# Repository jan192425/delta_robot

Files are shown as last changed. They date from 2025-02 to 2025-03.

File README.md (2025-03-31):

# Aufbau einer Compliant-Delta-Kinematik für die intuitive Interaktion mit einem Mobilen Roboter

Nachfolgend ist die Projektarbeit von Jan Sopejstal, Thomas Tasler und Nick Müller beschrieben. Die Arbeit wurde im Wintersemester 24/25 an der Technischen Hochschule Nürnberg Georg Simon Ohm durchgeführt und von Herrn Prof. Dr. rer. nat. Christian Pfitzner betreut.

## Inhaltsverzeichnis

- [1. Projektbeschreibung / Ziel des Projektes](#1-projektbeschreibung--ziel-des-projektes)
- [2. Komponenten des Delta-Pickers](#2-komponenten-des-delta-pickers)
- [3. Auslegung der Motoren](#3-auslegung-der-motoren)
- [4. Umsetzung der zwei Modis](#4-umsetzung-der-zwei-modis)
    - [4.1 Setup](#41-setup)
    - [4.2 Auswählbare Modi](#42-auswählbare-modi)
        - [4.2.1 Punktnavigation (mode: 0)](#421-punktnavigation-mode-0)
        - [4.2.2 Compliant-Modus (mode: 1)](#422-compliant-modus-mode-1)
- [5. Simulator für Delta-Roboter](#5-simulator-für-delta-roboter)
---

## 1. Projektbeschreibung / Ziel des Projektes
Für die Steuerung eines mobilen Robotes soll eine Delta-Kinematik aufgebaut werden. Durch eine geeignete Auswahl an Motoren und Ansteuerung soll die Kinematik einen vorgegebenen Zielpunkt anfahren können. Darüber hinaus, soll die Kinematik auch durch Interaktion in eine Richtung von Hand bewegt werden und bei eine einem Loslassen zurück in die Ursprungsposition fahren. Notwendig ist hierfür eine dynamische Regelung.<br>
Eine Video, das den gesamten Projektverlauf dokumentiert, ist unter folgendem Link zu finden: https://www.youtube.com/watch?v=dIm20Sjufmg&ab_channel=ThomasT .

## 2. Komponenten des Delta-Pickers
Der Delta-Roboter besteht grundlegend aus einer [Grundplatte](/images/base.png), [drei Baugleichen Armen](/images/arm.png) sowie einer [Endeffektorplatte](/images/endeffektor.png). An der [Grundplatte](/images/base.png) werden zudem die Motorhalterungen sowie ein Gehäuse montiert. Das Gehäuse dient zur Befestigung von Bauteilen, welche für die Ansteuerung der Motoren erforderlich sind. Nachfolgend ist der Gesamtaufbau dargestellt.

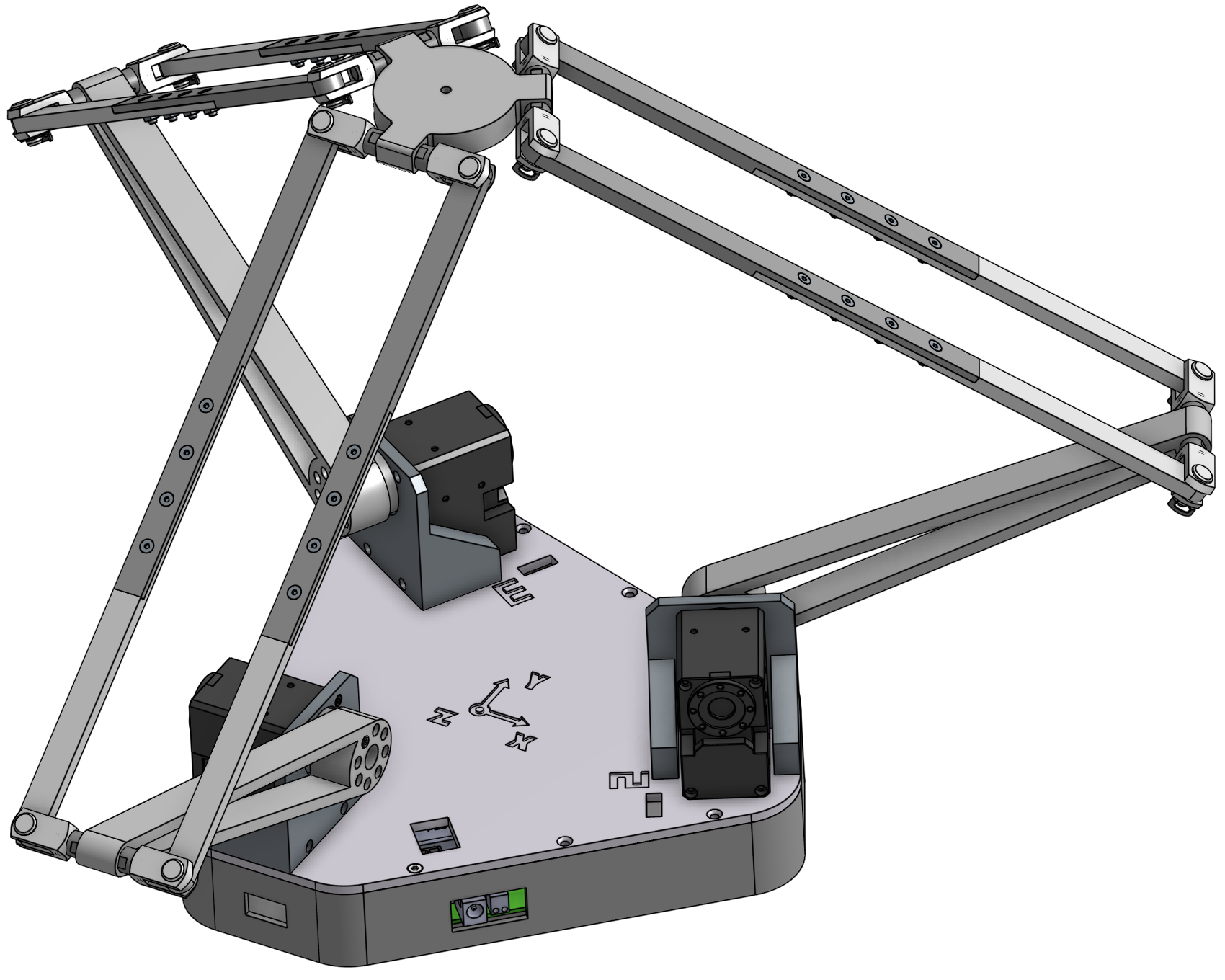
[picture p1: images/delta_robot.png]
Delta_Roboter


Die nicht zugekauften Bauteile des Delta Roboters sind als [stl Dateien](/stl/) abgelegt. In der folgenden Tabelle sind die für die Montage erfolgerlichen Komponenten aufgelistet. Darin enhalten sind sowohl die Zukaufkaufteile als auch die notwendige Anzahl der jeweiligen stl-Datei.

|**Bauteil - Zukauf**|**Stückzahl**|
|---|:---:|
|Dynamixel XM540-W270-R|3|
|ROBOTIS DYNAMIXEL U2D2 Power Hub|1|
|ROBOTIS DYNAMIXEL U2D2|1|
|Gabelkopf DIN 71752 6x12|12|
|Bolzen für Gabelkopf ø6mm|12|
|Gewindestange M6x1x41.5|6|
|Zylinderschraube mit Innensechskant ISO 4762 M2,5 x 25|24|
|Senkschraube mit Innensechsrund ISO 14581 M3 x 16|15|
|Senkschraube mit Innensechsrund ISO 14581 M3 x 10|24|
|Sechskantmuttern DIN 934 M3|24|
|M3 Schmelzgewindeeinsatz|15|
|DYNAMIXEL Kabel X4P 300mm|3|
|DYNAMIXEL Kabel X4P 100mm|1|
|||
|**Bauteil - nicht Zukauf**|**Stückzahl**|
|[base housing](/stl/base_housing.stl)|1|
|[base plate](/stl/base_plate.stl)|1|
|[bicep rod](/stl/bicep_rod.stl)|3|
|[end effector base](/stl/end_effector_base.stl)|1|
|[forarm rod divided 1](/stl/forarm_rod_divided_1.stl)|6|
|[forarm rod divided 2](/stl/forarm_rod_divided_2.stl)|6|
|[motor mount](/stl/motor_mount.stl)|3|

## 3. Auslegung der Motoren

Für die Auswahl der Motoren ist das maximal auftretende Drehmoment und die maximale Drehzahl von Bedeutung. Da der Delta-Roboter eine geschlossene Kinematik besitzt ist die Berechnung insbesondere für den dynamischen Fall von hoher Komplexität. Aus diesem Grund wurde nur der statische Fall betrachtet und das Ergebnis mit einem Sicherheitsfaktor verrechnet.

Die Berechnung des maximal auftretenden Drehmoments erfolgt mithilfe eines [Matlab Skripts](/matlab/delta_picker_motorenauslegung.mlx). Dadurch ist es möglich, die Motormomente für jede Effektorposition im Arbeitsraum zu ermitteln. Für eine statische Last von etwa 4.0 kg auf den Endeffektor ergeben sich die folgenden Motormomente.

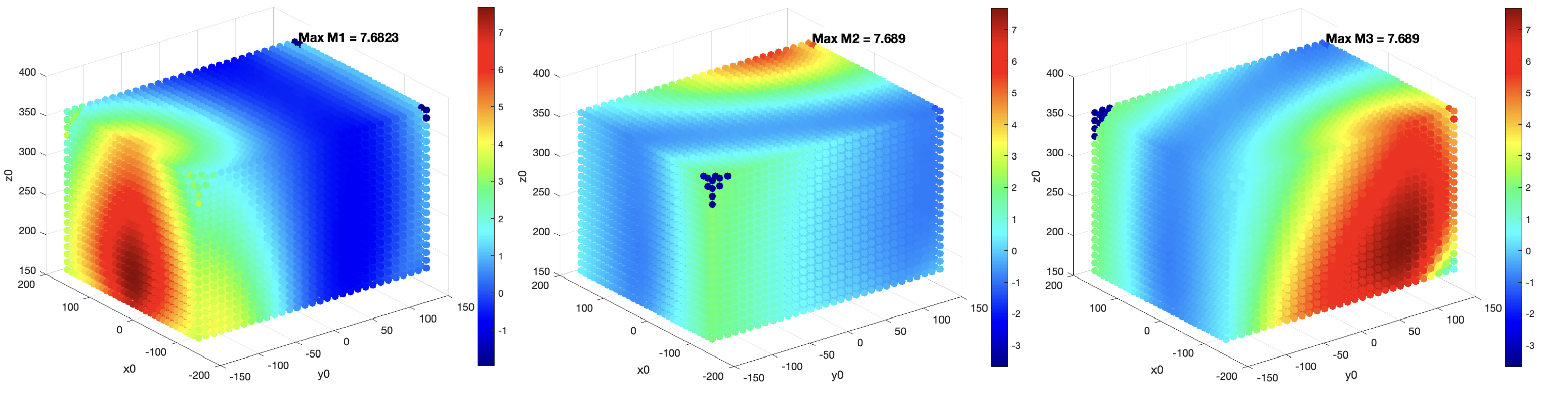
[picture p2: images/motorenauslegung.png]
Motormomente


Das maximal erforderliche Motormoment errechnet sich somit zu 7.6 Nm. Der DYNAMIXEL XM540-W270-R kann ein Drehmoment von bis zu 12.9 Nm aufbringen. Des Weiteren verfügen DYNAMIXEL Motoren über eine integrierte Regelung und ein dazu passendes Software Development Kit. Aufgrund dieser Vorteile wurde der oben genannte DYNAMIXEL anstelle eines konventionellen Motors ausgewählt.

## 4. Robotersteuerung mit ROS2
Die Kommunikation zwischen Motoren und Computer erfolgt in diesem Projekt mittels ROS2.

### 4.1 Setup
Für die Ansteuerung des Delta-Roboters müssen folgende Schritte zur Vorbereitung gemacht werden:
1.  Download des DynamixelSDK-Repositorys:
```
git clone https://github.com/ROBOTIS-GIT/DynamixelSDK.git
```
2. Download des delta_robot-Repositorys 
```
git clone https://github.com/jan192425/delta_robot.git
```
3. Installieren der Packete
```
colcon build 
```
4. sourcen der setup.bash Datei
```
source install/setup.bash
```
5. Starten der Nodes in einzelnen Terminals 
```
ros2 run delta_robot opmod_node
```
```
ros2 run delta_robot commot_node
```
**Hinweis:** <br> Erst das Starten der COMMOT Node setzt den Torque_enable der Motoren auf 1 (Bestromung der Motoren). **=> Arme fallen herunter wenn COMMOT Node gestoppt wird!!**

### 4.2 Auswählbare Modi
Im Rahmen dieses Projektes soll der Delta-Roboter über zwei Modi verfügen. Erstens einen Modus zur Punktnavigation, d.h. der Anwender gibt eine Position des Endeffektors im Arbeitsraum vor. Durch Berechnung der inversen Delta-Kinematik können die erforderlichen Motorwinkel ermittelt und mitteles eines Regelkreises eingestellt werden. 

Des Weiteren soll ein Compliant-Modus implementiert werden. Der Endeffektor soll durch den Anwender ausgelenkt werden können und beim Loslassen wieder in den Ursprung zurückfahren. Wenn der Effektor zu einem gewissen Grad aus der Mitte gelenkt ist, soll diese Information an den Mobilen Roboter weitergeleitet werden. Dieser soll als Reaktion hierauf sich - und dadurch auch das Zentrum der Delta-Grundplatte- wieder unter den Endeffektor bewegen. 

Zwischen den zwei Modi kann mit dem Nachrichten-Typ *OpMod* hin-und hergeschaltet werden. Dieser Nachrichten-Typ ist selbst definiert und im package delta_robot_interfaces [delta_robot_interfaces](/src/delta_robot_interfaces/msg/OpMod.msg)zu finden. Im Folgenden werden beide Modi und deren Struktur in ROS2 anhand von Bildern vorgestellt. 

#### 4.2.1 Punktnavigation (mode: 0)
Für die Aktivierung des Punktnavigationsmodus muss (nach Start der 2 Nodes) folgende Nachricht publiziert werden, wobei an den ... Stellen die gewünschte Endeffektorposition anzugeben ist:
- in neuem Terminal:
```
source install/setup.bash
```
```
ros2 topic pub -1 OpMod delta_robot_interfaces/OpMod "{mode: 0, xeff: ..., yeff: ..., zeff: ...}"
```
**Hinweis:** <br>
Die Ausrichtung des Koordinatensystems ist auf der Grundplatte des Delta-Roboters zu finden.

Für den Fall, dass der vorgegebene Punkt aufgrund der Geometrie und der daraus resultierenden Kinematik des Roboters nicht zu erreichen ist, verharrt der Delta-Roboter auf der letzten zulässigen Position. Der Roboter wird ebenfalls in der letzten Position verharren, wenn die gewünschte Effktorposition Motorwinkel <= -30° oder >=90° bedeuten würden. Dadurch wird im ersten Fall die Kollision mit der Grundplatte verhindert. Im zweiten Fall wird so die kinematische Singularität der Delta-Kinematik verhindert, die aus der bei 90° parallel zueinander stehenden  Bicepsgliedern resultieren würde.

Die untenstehende Abbildung zeigt den Datenfluss zwischen den ROS2 Nodes COMMOT und OPMOD, der ausgelagerten Kinematikberechnung und den Motoren. Dabei steht T für das Terminal bzw. die dort publizierte *OpMod* Nachricht. Weiterhin ist zu erkennen, dass sich die Regelparamter in COMMOT Node verändern lassen für den Fall, dass das aktuell implementierte Verhalten der Positionsregelung für die sepezifische Anwendung angepasst werden muss.

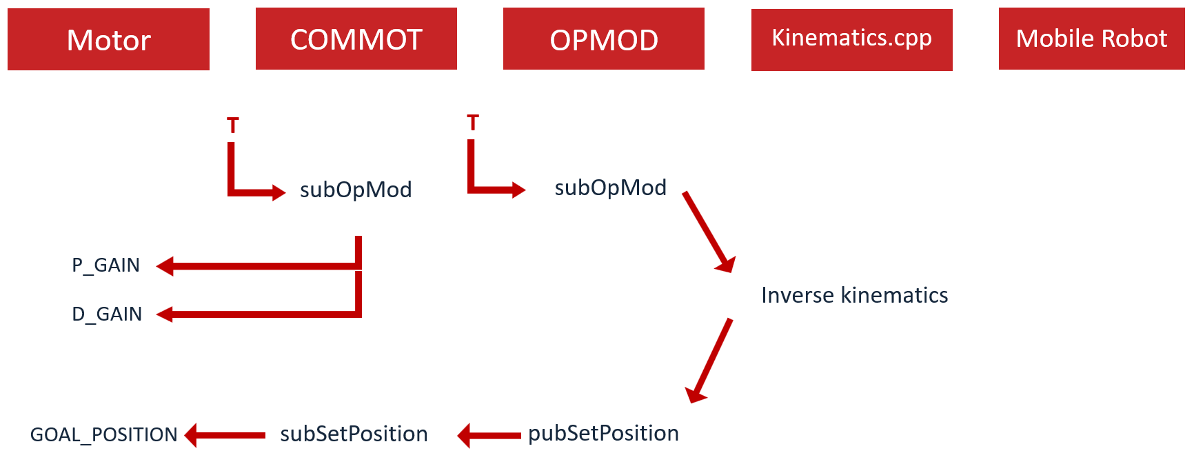
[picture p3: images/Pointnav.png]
Punktnavi


#### 4.2.2 Compliant-Modus (mode: 1)
**Umsetzung des "compliant behaviours":** <br>
Die Realisierung eines Roboters mit nachgiebigen Verhaltens (engl. "compliant behaviour") bedarf der Herleitung des komplexen Dynamiksystems der closed-loop Delta-Kinematik und einer Regelung, die in den meisten Fällen eine Drehmomentüberwachung benötigt. Da Motoren mit integrierter Drehmomentüberwachung i.d.R. ein Vielfaches mehr kosten, sollte im Rahmen dieses Projekts untersucht werden, ob man ein ähnliches Verhalten auch mit Motoren ohne Drehmomentüberwachung und ohne die teils nur numerisch mögliche Modellrechnung realsieren kann.

Der Ansatz, der hierbei verfolgt wurde, sieht eine adaptive Änderung des P-Gains in Abhängigkeit der individuellen Positions-Regeldifferenz der 3 Motoren vor. Dafür wird zunächst feste Zielpositionen für alle 3 Motoren festgelegt, die zu Endeffektorposition von (0|0|300) führen.<br> 
Eine Änderung des Motor-P-Gains ist gleichbedeutend mit der wahrnehmbaren Steifigkeit des Motors, wenn dieser manuell aus seiner Zielposition ausgelenkt wird. Durch das adaptive Ändern des P-Gains lässt sich so das Moment des Motors in Abhängigkeit dem radialen Weg indirekt beeinflussen. <br>
Für diese Abhängigkeit wurden verschiedene Formen getestet, wie in der Abbildung unten zu sehen ist. Die aktuell im Code verwendte Abhänigigkeit ist die der grünen Geraden. Diese Abhängigkeit entpricht auch der Intuition, da das oben beschriebne Verhalten sehr an eine Federkennlinie erinnern lässt. Als Optimierung der Geraden ist die orangene Kurve aufzufassen. Diese besteht aus der Überlagerung einer Geraden und einer e-Funktion. Die Idee hinter dieser Kombination ist, das P-Gain an den Grenzen des zulässigen Arbeitsbereichs so hoch zu setzen, dass jenes den Arbeitsbreich indirekt und v.a. weicher als eine reine if-Bedingung begrenzt. Die Parameter dieser Funktion benötigen allerdings noch Anpassung. 

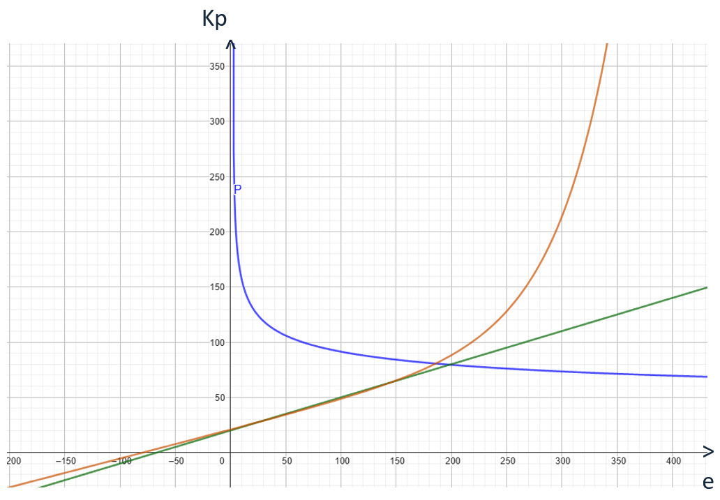
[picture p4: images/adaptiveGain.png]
adapKoeff


**Disclaimer:** <br> 
Aktuell ist die adaptive Regleranpassung im Code auskommentiert. Die Funktionalität des Codes ist zwar gegeben, allerdings ist aktuell die Zuverlässigkeit im langfristigen Betrieb noch nicht gesichert. Details hierzu finden sich in den Kommentaren in der [commot_node.cpp](/src/delta_robot/src/commot_node.cpp) (Zeilen 215-218).<br> 
Um die Zuverlässigkeit zu gewährleisten ist aktuell ein konstantes P-Gain implementiert. Dies sorgt zwar für ein generell sehr weiches Verhalten und eine gute Zentrierung in den Ursprung bzgl. der x-y-Ebene, jedoch gleichzeitig auch für eine große Ungenauigkeit bzgl. der Z-Koordinate. Diese Abweichung existiert auch mit adaptiver Regleranpassung aber in wesentlich geminderter Form.

**ROS2 Struktur des Compliant-Modus:**<br>
In der Abbildung unterhalb des Absatzes ist der Datenfluss für den Compliant-Mode dargestellt. Wie bereits beim Punktnavigationsmodus erwähnt, wird auch hier der Start des Modus über das Publizieren einer *OpMod*-Nachricht im Terminal (T) in­i­ti­ie­rt, wobei mit dem Zusatz -r eine Publikationsfrequenz eingestellt werden muss. Mit dieser Frequenz wird einerseits die aktuelle Position des Endeffektors kontinuierlich berechnet und andererseits die aktuellen P-Gains für den Fall der adaptiven Regelparameter-Veränderung.<br> 
Die COMMOT Node verändert nach Empfang der Nachricht die P- und D-Gains der Motoren (entweder zu anderen Konstantwerten oder adaptiv). Die OPMOD Node stellt parallel einen service request an die COMMOT Node, um die aktuelle Position der Motoren zu erhalten. Wurden die Positionen empfangen, wird die direkte Kinematik berechnet und das Ergbnis über eine TimerCallback als Twist-Nachricht publiziert.<br>
Das Publizieren in einer TimerCallback ist notwendig, da die dem Projekt zur Verfügung stehende mobile Plattform eine gewisse Frequenz an Twist-Nachrichten braucht, um ein flüssiges Drehen der Räder zu gewährleisten. Diese Frequenz ist allerdings so hoch, dass es bei der Verwendung dieser bei der Effektorpositionsbestimmung zu Kommunikationsfehlern während des Present Position services kommt. Daher wird das Publizieren der Twist Nachricht vom Rest des Compliant-Modes mit Hilfe der TimerCallback zeitlich entkoppelt.

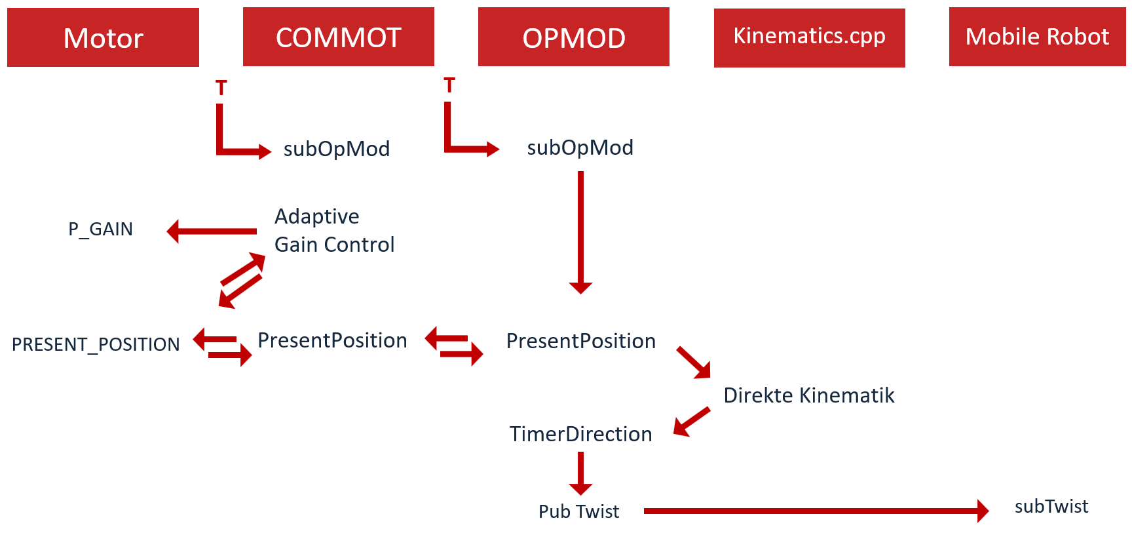
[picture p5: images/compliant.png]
comp


Für die Aktivierung des Compliant - Modus sind folgende Schritte erforderlich
- in neuem Terminal:
```
source install/setup.bash
```
```
ros2 topic pub -r 2 OpMod delta_robot_interfaces/OpMod "{mode: 1}"
```
**Hinweis:** <br>
Die Regelparameter lassen sich in [commot_node.cpp](/src/delta_robot/src/commot_node.cpp) in Zeile 216 (P-Gain) und 225 (D-Gain) anpassen.<br>
Die Frequenz von 2 Hz dient, wie bereits erwähnt für die kontinuierliche Berechnung der Effektorposition und nicht zum Publizieren der Twist Nachrichten. Um die Twist-Frequenz zu verstellen, muss die Periodendauer des Timers in der OPMOD Node [opmod_node.cpp](/src/delta_robot/src/opmod_node.cpp) (Zeile 50) angepasst werden.

## 5. Simulator für Delta-Roboter

Außerdem wurde während der Projektarbeit ein Simulator für den Delta-Roboter aufgebaut. Dafür wurde zu Beginn Gazebo genutzt. Da dies nun nichtmehr unterstützt wird, wurde auf die neue Umgebung Iginition gewechselt. ALle notwendigen Datein sind im [delta_robot_ros2](/src/delta_robot_ros2/) Package abgelegt. Außerdem müssen die Schritte aus Abschnitt 4.1 durchgeführt werden, um die Simulation zu starten.

Für das Starten der Iginition Umgebung ist folgender Befehl auszuführen
```
ros2 launch delta_robot_gazebo delta_robot_bringup_gazebo.launch.py
```

Für das Starten der Gazebo Umgebung ist folgender Befehl auszuführen
```
ros2 launch delta_robot_gazebo delta_robot_bringup_classic_gazebo.launch.py
```

**Anmerkung:** <br>
Der hier aufgebaute Simulator stellt nur ein Grundgerüst dar. Insbesondere hinsichtlich der closed-loop-Kinematik muss der Simulator noch ausgearbeitet werden. Zum Zeitpunkt der Projektarbeit wurde hierfür noch keine passende Lösung gefunden. Außerdem ist auch noch ein Skript zu schreiben, mit welchem die Arme bewegt werden können. Derzeit können die Arme des Delta Roboters nur direkt innerhalb der Simulationsumgebung über den "Joint position Controller" gesteuert werden.

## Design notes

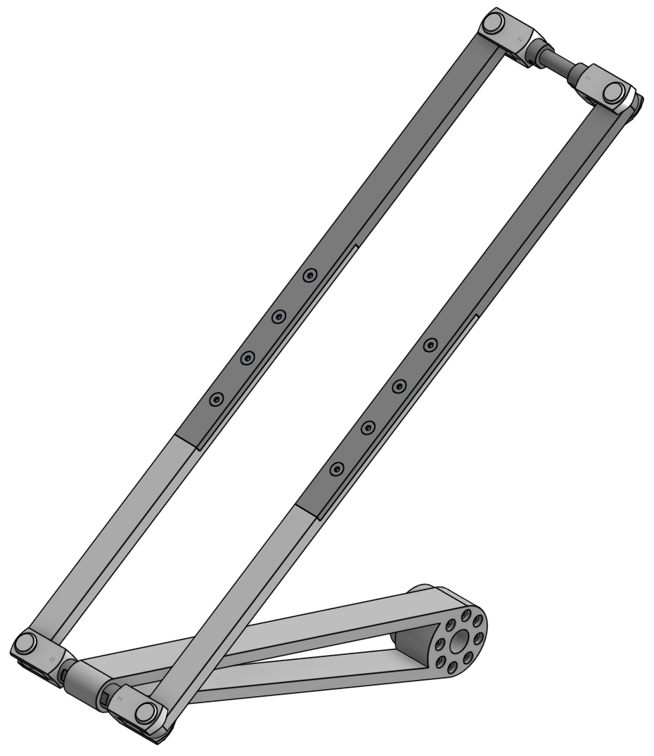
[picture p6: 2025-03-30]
images/arm.png

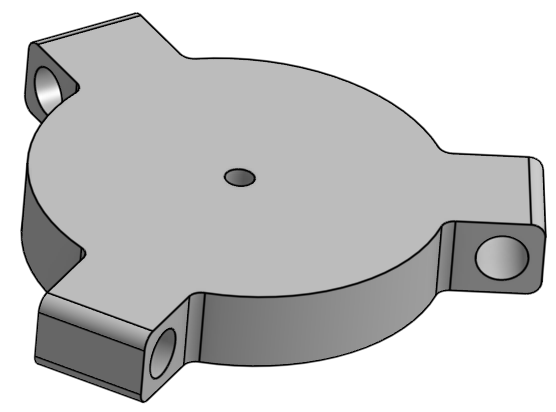
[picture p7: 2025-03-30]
images/endeffektor.png

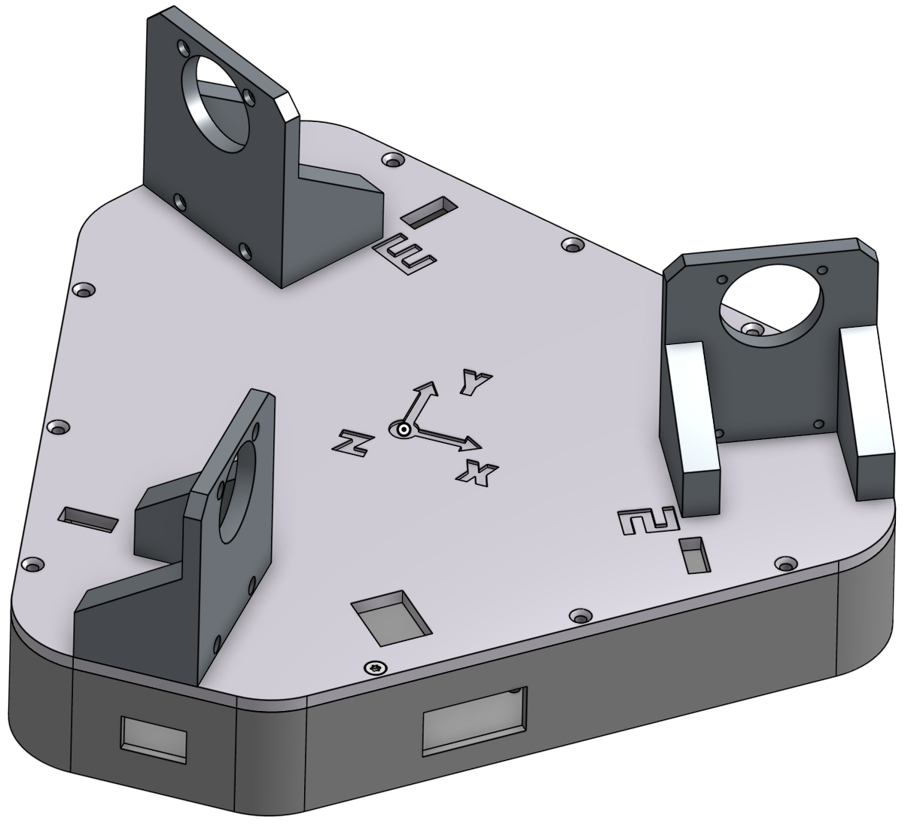
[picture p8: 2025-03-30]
images/base.png

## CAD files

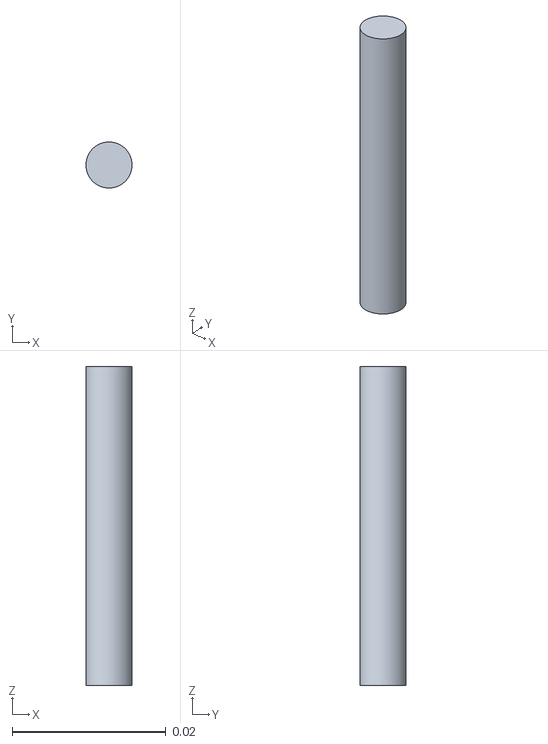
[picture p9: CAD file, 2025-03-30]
src/delta_robot_ros2/delta_robot_description/meshes/delta_robot/connecting_element.stl
0.006 x 0.006 x 0.0415

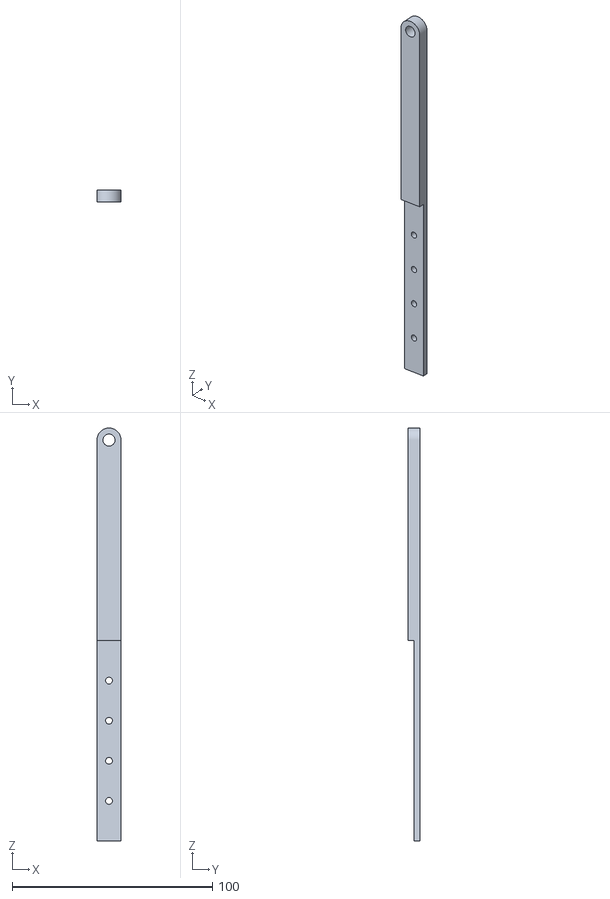
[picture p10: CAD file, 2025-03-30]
stl/forarm_rod_divided_1.stl
12.0 x 6.00 x 206.0

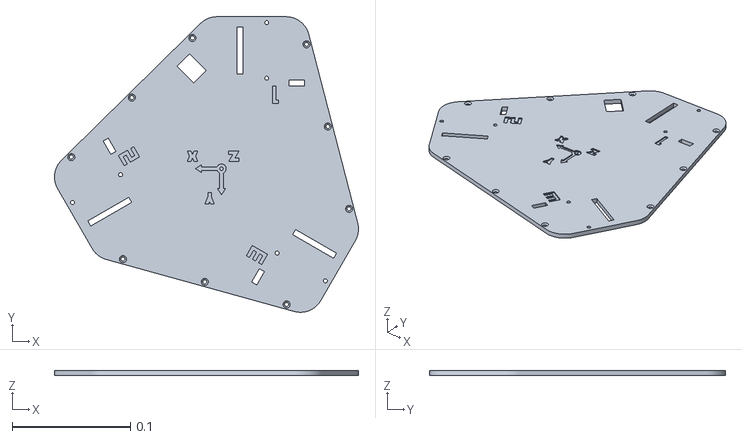
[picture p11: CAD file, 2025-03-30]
src/delta_robot_ros2/delta_robot_description/meshes/delta_robot/base_plate.stl
0.257 x 0.25 x 0.004

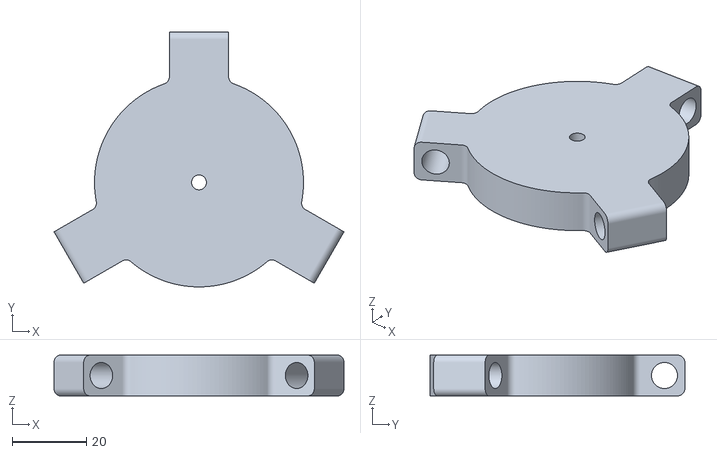
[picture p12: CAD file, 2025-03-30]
stl/end_effector_base.stl
78.1 x 68.7 x 11.0

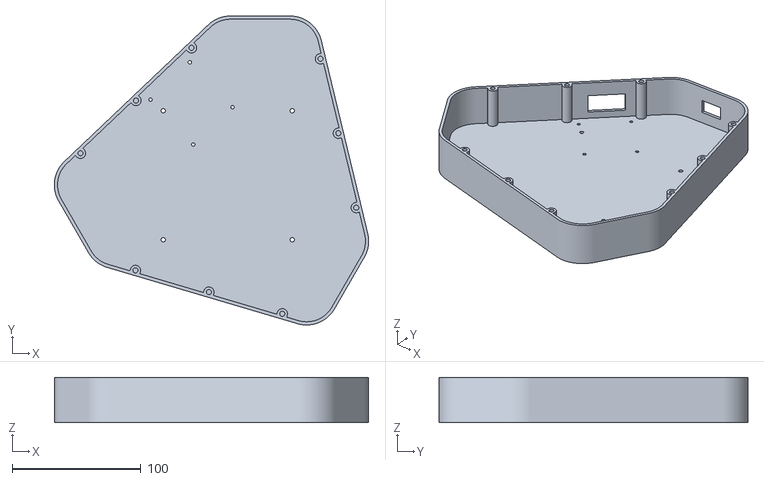
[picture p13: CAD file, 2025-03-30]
stl/base_housing.stl
243.7 x 239.6 x 35.0

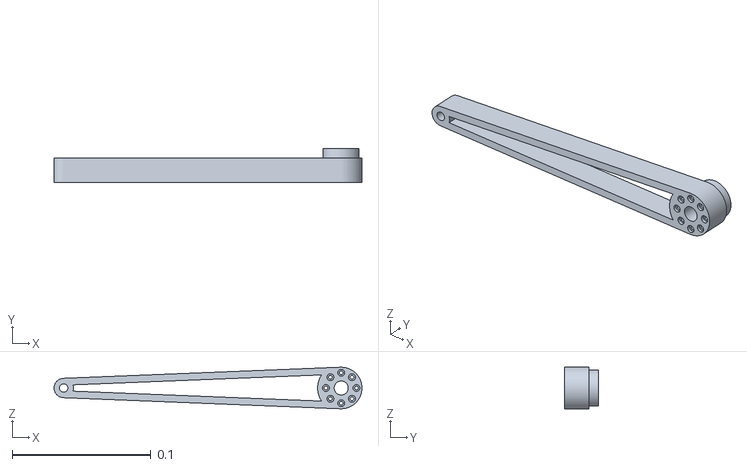
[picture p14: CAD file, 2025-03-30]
src/delta_robot_ros2/delta_robot_description/meshes/delta_robot/bicep_rod.stl
0.222 x 0.0245 x 0.03

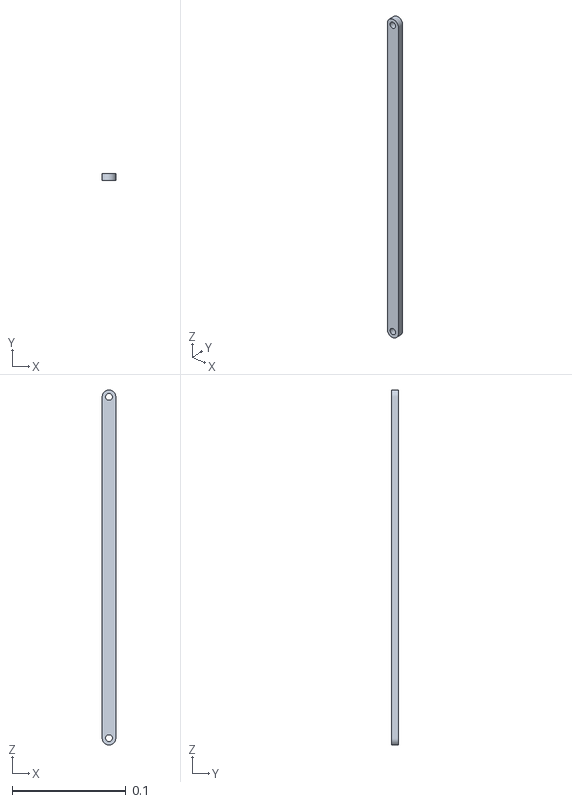
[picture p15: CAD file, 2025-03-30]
src/delta_robot_ros2/delta_robot_description/meshes/delta_robot/forarm_rod.stl
0.012 x 0.006 x 0.312

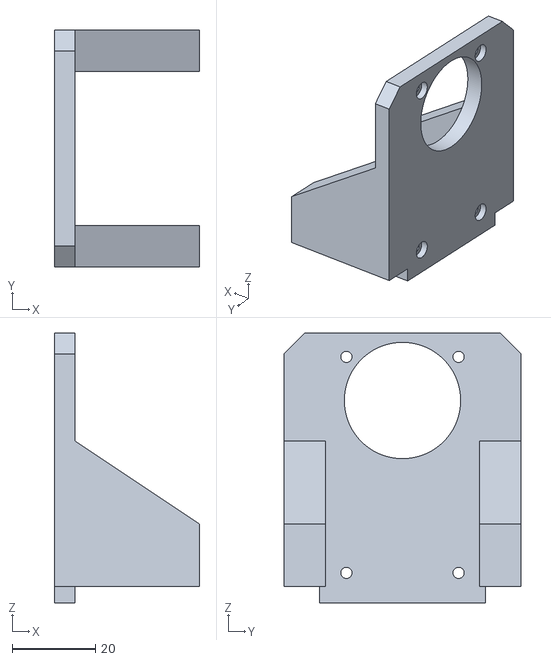
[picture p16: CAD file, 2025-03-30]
stl/motor_mount.stl
35.0 x 57.0 x 65.0

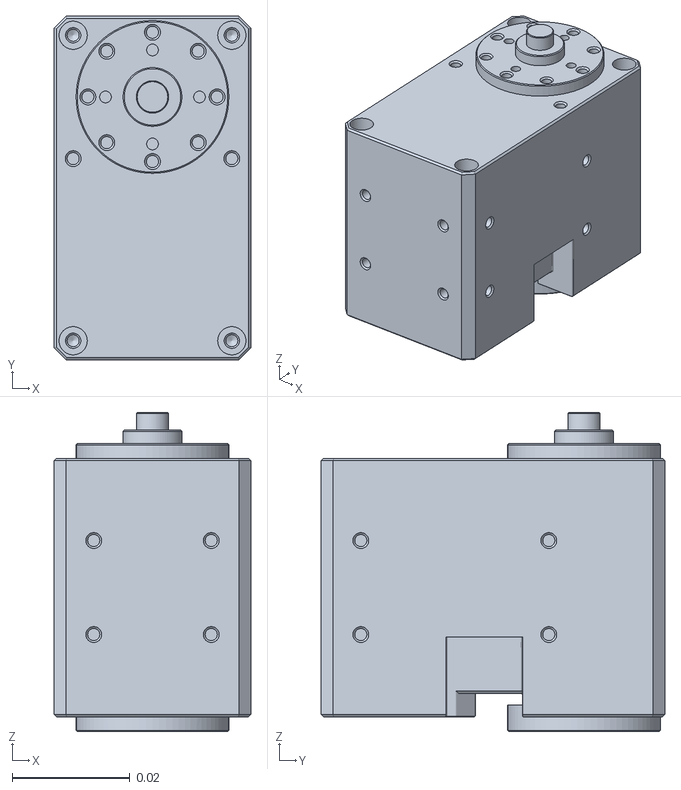
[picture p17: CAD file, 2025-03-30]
src/delta_robot_ros2/delta_robot_description/meshes/delta_robot/dc13_x540_dummy.stl
0.0335 x 0.0585 x 0.0543

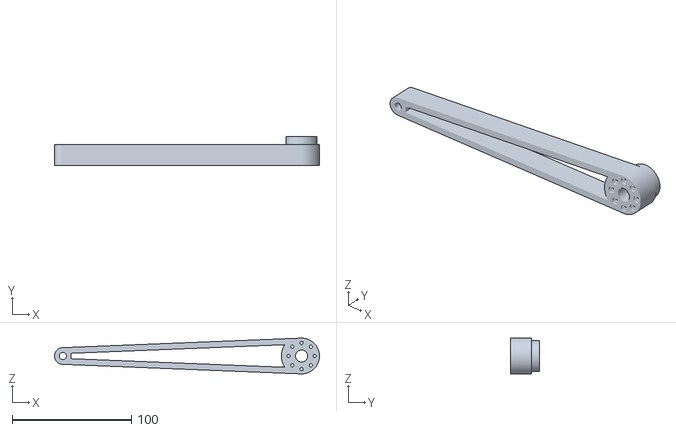
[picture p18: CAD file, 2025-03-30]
stl/bicep_rod.stl
222.0 x 24.5 x 30.0

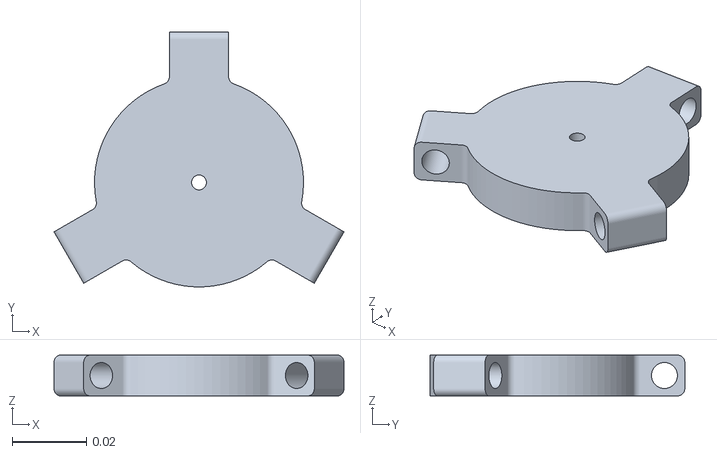
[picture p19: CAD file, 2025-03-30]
src/delta_robot_ros2/delta_robot_description/meshes/delta_robot/end_effector_base_v02.stl
0.0781 x 0.0686 x 0.011

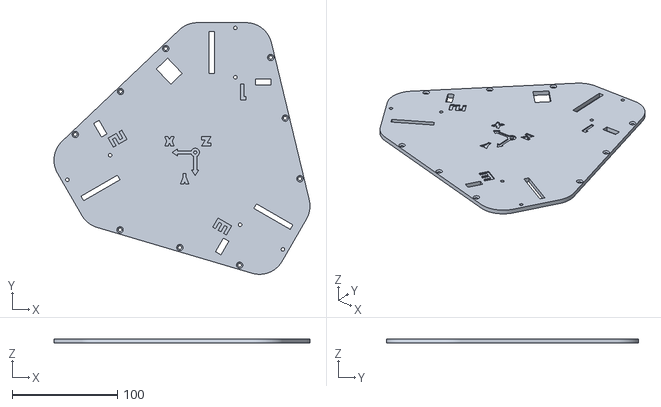
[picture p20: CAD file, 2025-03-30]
stl/base_plate.stl
243.7 x 239.6 x 4.00

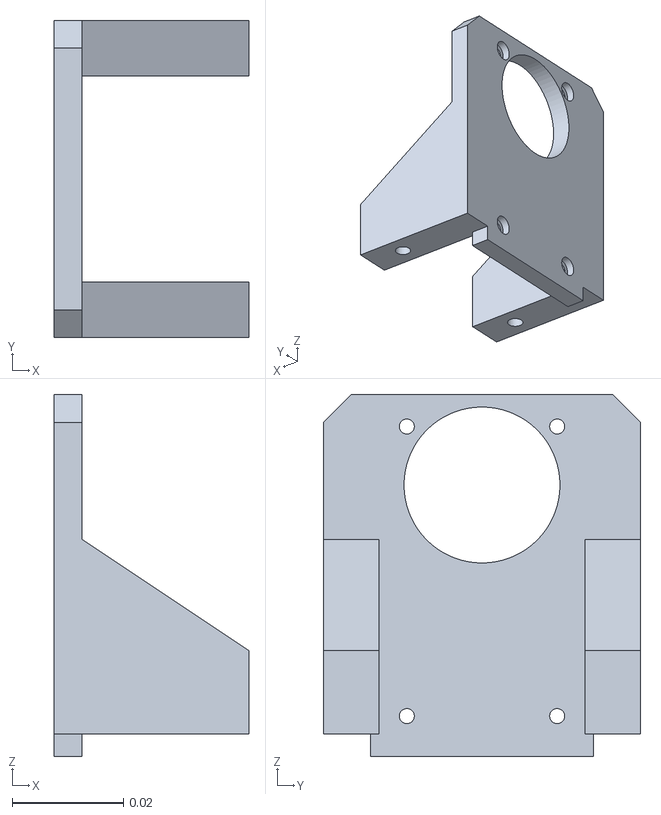
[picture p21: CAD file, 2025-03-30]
src/delta_robot_ros2/delta_robot_description/meshes/delta_robot/motor_mount.stl
0.035 x 0.057 x 0.065

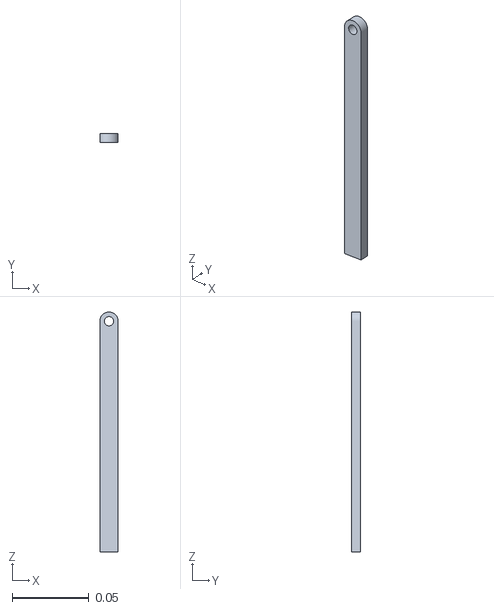
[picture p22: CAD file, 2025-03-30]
src/delta_robot_ros2/delta_robot_description/meshes/delta_robot/forarm_rod_half.stl
0.012 x 0.006 x 0.156

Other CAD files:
stl/forarm_rod_divided_2.stl
src/delta_robot_ros2/delta_robot_description/meshes/delta_robot/connecting_element_half.stl
src/delta_robot_ros2/delta_robot_description/meshes/delta_robot/63755205_2.stl
src/delta_robot_ros2/delta_robot_description/meshes/delta_robot/63755205_3.stl
src/delta_robot_ros2/delta_robot_description/meshes/delta_robot/63755205_1.stl

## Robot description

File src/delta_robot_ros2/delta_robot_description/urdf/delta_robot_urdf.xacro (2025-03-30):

<?xml version="1.0"?>
<robot xmlns:xacro="http://www.ros.org/wiki/xacro" name="delta_robot">

    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

    <link name = "world"></link>

    <joint name="base_joint" type="fixed">
        <origin xyz="0.2 0.2 0.002" rpy="0 0 0"/>
        <parent link="world"/>
        <child link="base_link"/>        
    </joint>

    <link name="base_link">
    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
    <inertial>
    <origin xyz="-0.00016122483469887020305 0.00055229382476998899187 0.030796178444245096012" rpy="0 0 0"/>
    <mass value="2.2633912012388961443" />
    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
    </inertial>
    </link>


    <link name="bicep_rod">
    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
    <inertial>
    <origin xyz="-0.078081968111977914648 -8.4155794501061477637e-17 -0.014997482893929825476" rpy="0 0 0"/>
    <mass value="0.050961850551235823858" />
    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
    </inertial>
    </link>


    <link name="connecting_element">
    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
    <inertial>
    <origin xyz="-1.3905153366695095013e-08 -2.308353284840540696e-17 -1.8807546362910670964e-18" rpy="0 0 0"/>
    <mass value="0.043235391457957531025" />
    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
    </inertial>
    </link>


    <link name="forarm_rod">
    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
    <inertial>
    <origin xyz="2.0380347027211559199e-17 0.14999999999999993894 -0.0030000000000000052666" rpy="0 0 0"/>
    <mass value="0.023080135190930266276" />
    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
    </inertial>
    </link>


    <link name="closing_arm1_1">
    <inertial>
    <origin xyz="0 0 0" rpy="0 0 0" />
    <mass value="1e-9" />
    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
    </inertial>
    </link>
    <joint name="closing_arm1_1_frame" type="fixed">
    <origin xyz="-3.4694469519536141888e-18 0.29999999999999993339 0" rpy="-6.1343203009518076313e-33 1.5123475901484657517e-33 -1.1256002290908234313e-17" />
    <parent link="forarm_rod" />
    <child link="closing_arm1_1" />
    <axis xyz="0 0 0"/>
    </joint>


    <joint name="12_passive" type="revolute">
    <origin xyz="-1.5959455978986625269e-16 0.0030000000000003912426 0.032749999999999980516" rpy="1.570796326794896558 -1.3312356219938219493 3.1415926535897855665" />
    <parent link="connecting_element" />
    <child link="forarm_rod" />
    <axis xyz="0 0 1"/>
    <limit effort="1" velocity="20" lower="-0.52359877559829881566" upper="0.52359877559829881566"/>
    <joint_properties friction="0.0"/>
    </joint>


    <link name="forarm_rod_2">
    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
    <inertial>
    <origin xyz="2.0380347027211559199e-17 -0.1500000000000000222 -0.0030000000000000603441" rpy="0 0 0"/>
    <mass value="0.023080135190930266276" />
    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
    </inertial>
    </link>


    <link name="connecting_element_2">
    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
    <inertial>
    <origin xyz="0.032749999999999550304 1.3905153363353280375e-08 0.0030000000000000425632" rpy="0 0 0"/>
    <mass value="0.043235391457957531025" />
    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
    </inertial>
    </link>


    <link name="closing_arm1_2">
    <inertial>
    <origin xyz="0 0 0" rpy="0 0 0" />
    <mass value="1e-9" />
    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
    </inertial>
    </link>
    <joint name="closing_arm1_2_frame" type="fixed">
    <origin xyz="0.065499999999998892442 0 1.1102230246251565404e-16" rpy="3.141592653589793116 -3.0701093824491574819e-23 2.4767203673916650163e-17" />
    <parent link="connecting_element_2" />
    <child link="closing_arm1_2" />
    <axis xyz="0 0 0"/>
    </joint>


    <joint name="14_passive" type="revolute">
    <origin xyz="-1.3877787807814456755e-17 -0.29999999999999993339 5.5511151231257827021e-17" rpy="-3.141592653589793116 -3.3246881643796303939e-19 -2.9020319487887582532" />
    <parent link="forarm_rod_2" />
    <child link="connecting_element_2" />
    <axis xyz="0 0 1"/>
    <limit effort="1" velocity="20" lower="-0.52359877559829881566" upper="0.52359877559829881566"/>
    <joint_properties friction="0.0"/>
    </joint>


    <joint name="13_passive" type="revolute">
    <origin xyz="-1.6653345369377348106e-16 0.0030000000000002802203 -0.032749999999999966638" rpy="-1.570796326794896558 1.3312356219938281665 -7.7545827997474715894e-15" />
    <parent link="connecting_element" />
    <child link="forarm_rod_2" />
    <axis xyz="0 0 1"/>
    <limit effort="1" velocity="20" lower="-0.52359877559829881566" upper="0.52359877559829881566"/>
    <joint_properties friction="0.0"/>
    </joint>


    <joint name="11_wheel" type="continuous">
    <origin xyz="-0.2000000000000002609 -2.0122792321330962295e-16 -0.015749999999999979294" rpy="-1.8262551998394623635e-15 2.3272302527077074766e-16 -1.5627224950883411569" />
    <parent link="bicep_rod" />
    <child link="connecting_element" />
    <axis xyz="0 0 1"/>
    <limit effort="1" velocity="20" />
    <joint_properties friction="0.0"/>
    </joint>


    <joint name="motor_1" type="revolute">
    <origin xyz="0.015572484711309449862 0.10059761139126591201 0.048749999999999987788" rpy="-1.57079632679489678 -0.0080738317065514441512 -1.5707963267948947816" />
    <parent link="base_link" />
    <child link="bicep_rod" />
    <axis xyz="0 0 1"/>
    <limit effort="1" velocity="20" lower="-0.52359877559829881566" upper="1.570796326794896558"/>
    <joint_properties friction="0.0"/>
    </joint>


</robot>

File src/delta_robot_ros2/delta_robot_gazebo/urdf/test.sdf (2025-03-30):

<?xml version="1.0"?>
<sdf version='1.9'>
  <model name='delta_robot'>
    <joint name='base_joint' type='fixed'>
      <pose relative_to='__model__'>0.2 0.2 1 0 0 0</pose>
      <parent>world</parent>
      <child>base_link</child>
    </joint>
    <link name='base_link'>
      <pose relative_to='base_joint'>0 0 0 0 0 0</pose>
      <inertial>
        <pose>-0.0001612248346988456 0.0005522938247699926 0.0307961784442451 0 0 0</pose>
        <mass>2.263391201238897</mass>
        <inertia>
          <ixx>0.013699240615172069</ixx>
          <ixy>-2.8956553318737741e-06</ixy>
          <ixz>1.0541336563790759e-06</ixz>
          <iyy>0.013707418413198559</iyy>
          <iyz>-2.9603162574548002e-06</iyz>
          <izz>0.02587911249136568</izz>
        </inertia>
      </inertial>
      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
    </link>
    <joint name='motor_1' type='revolute'>
      <pose relative_to='base_link'>0.01557248471130945 0.1005976113912659 0.04874999999999999 -1.570796326794897 0.1835764877121942 -1.5707963267949</pose>
      <parent>base_link</parent>
      <child>bicep_rod</child>
      <axis>
        <xyz>0 0 1</xyz>
        <limit>
          <lower>0</lower>
          <upper>1.570796326794897</upper>
          <effort>2000</effort>
          <velocity>2</velocity>
        </limit>
        <dynamics>
          <damping>0.050000000000000003</damping>
          <friction>0.050000000000000003</friction>
          <spring_reference>0</spring_reference>
          <spring_stiffness>0</spring_stiffness>
        </dynamics>
      </axis>
    </joint>
    <link name='bicep_rod'>
      <pose relative_to='motor_1'>0 0 0 0 0 0</pose>
      <inertial>
        <pose>-0.07808196811197794 -9.025725672866032e-17 -0.01499748289392982 0 0 0</pose>
        <mass>0.050961850551235831</mass>
        <inertia>
          <ixx>5.2079917158922497e-06</ixx>
          <ixy>-1.0521852075132921e-20</ixy>
          <ixz>-2.994417264727556e-06</ixz>
          <iyy>0.0002416605243036785</iyy>
          <iyz>-9.8620279913835896e-23</iyz>
          <izz>0.00024357414644567959</izz>
        </inertia>
      </inertial>
      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
    </link>
    <joint name='11' type='revolute'>
      <pose relative_to='bicep_rod'>-0.2 -1.387778780781446e-17 -0.01575 -1.343125022233315e-15 -3.537121670188392e-15 -0.844987181203198</pose>
      <parent>bicep_rod</parent>
      <child>connecting_element</child>
      <axis>
        <xyz>0 0 1</xyz>
        <limit>
          <effort>1</effort>
          <velocity>20</velocity>
          <lower>-10000000000000000</lower>
          <upper>10000000000000000</upper>
        </limit>
        <dynamics>
          <damping>0.050000000000000003</damping>
          <friction>0.050000000000000003</friction>
          <spring_reference>0</spring_reference>
          <spring_stiffness>0</spring_stiffness>
        </dynamics>
      </axis>
    </joint>
    <link name='connecting_element'>
      <pose relative_to='11'>0 0 0 0 0 0</pose>
      <inertial>
        <pose>-1.390515342721101e-08 1.336635665596689e-17 -5.01534569677618e-18 0 0 0</pose>
        <mass>0.043235391457957517</mass>
        <inertia>
          <ixx>2.117953909382608e-05</ixx>
          <ixy>1.654388519189724e-09</ixy>
          <ixz>-7.7632988634472204e-21</ixz>
          <iyy>2.104782635777846e-05</iyy>
          <iyz>4.4464792328571068e-11</iyz>
          <izz>1.0143582146042339e-06</izz>
        </inertia>
      </inertial>
      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
    </link>
    <joint name='12' type='revolute'>
      <pose relative_to='connecting_element'>6.605826996519681e-15 0.002999999999999559 0.0327499999999999 -1.570796326794897 1.570796326794897 0</pose>
      <parent>connecting_element</parent>
      <child>forarm_rod</child>
      <axis>
        <xyz>0 0 1</xyz>
        <limit>
          <effort>1</effort>
          <velocity>20</velocity>
          <lower>-10000000000000000</lower>
          <upper>10000000000000000</upper>
        </limit>
        <dynamics>
          <damping>0.050000000000000003</damping>
          <friction>0.050000000000000003</friction>
          <spring_reference>0</spring_reference>
          <spring_stiffness>0</spring_stiffness>
        </dynamics>
      </axis>
    </joint>
    <link name='forarm_rod'>
      <pose relative_to='12'>0 0 0 0 0 0</pose>
      <inertial>
        <pose>1.338089576209312e-17 -0.15 -0.002999999999999978 0 0 0</pose>
        <mass>0.02308013519093027</mass>
        <inertia>
          <ixx>0.0001790752607307609</ixx>
          <ixy>-1.7841365676780891e-35</ixy>
          <ixz>-2.6158934878582789e-35</ixz>
          <iyy>3.4754053482994271e-07</iyy>
          <iyz>3.3312167309682231e-21</iyz>
          <izz>0.00017928432045444519</izz>
        </inertia>
      </inertial>
      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
    </link>
    <joint name='14' type='revolute'>
      <pose relative_to='forarm_rod'>0 -0.3 0 -3.141592653589793 1.740368768366112e-15 -2.618224693926866e-15</pose>
      <parent>forarm_rod</parent>
      <child>connecting_element_half</child>
      <axis>
        <xyz>0 0 1</xyz>
        <limit>
          <effort>1</effort>
          <velocity>20</velocity>
          <lower>-10000000000000000</lower>
          <upper>10000000000000000</upper>
        </limit>
        <dynamics>
          <damping>0.050000000000000003</damping>
          <friction>0.050000000000000003</friction>
          <spring_reference>0</spring_reference>
          <spring_stiffness>0</spring_stiffness>
        </dynamics>
      </axis>
    </joint>
    <link name='connecting_element_half'>
      <pose relative_to='14'>0 0 0 0 0 0</pose>
      <inertial>
        <pose>0.0128646317575684 -1.39051533011173e-08 0.003000064687584137 0 0 0</pose>
        <mass>0.021617696728978762</mass>
        <inertia>
          <ixx>5.0717910721166878e-07</ixx>
          <ixy>6.6564614349273319e-13</ixy>
          <ixz>-5.5752347028774129e-12</ixz>
          <iyy>2.0415297720126058e-06</iyy>
          <iyz>-8.3494347216414071e-10</iyz>
          <izz>1.9756734040792129e-06</izz>
        </inertia>
      </inertial>
      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
    </link>
    <joint name='arm_1_effector' type='revolute'>
      <pose relative_to='connecting_element_half'>0.03275000000000017 -2.275957200481571e-15 0.002999999999999808 -1.570796326794895 -0.6614106934910174 -1.5707963267949</pose>
      <parent>connecting_element_half</parent>
      <child>end_effector_base_v02</child>
      <axis>
        <xyz>0 0 1</xyz>
        <limit>
          <effort>1</effort>
          <velocity>20</velocity>
          <lower>-10000000000000000</lower>
          <upper>10000000000000000</upper>
        </limit>
        <dynamics>
          <damping>0.050000000000000003</damping>
          <friction>0.050000000000000003</friction>
          <spring_reference>0</spring_reference>
          <spring_stiffness>0</spring_stiffness>
        </dynamics>
      </axis>
    </joint>
    <link name='end_effector_base_v02'>
      <pose relative_to='arm_1_effector'>0 0 0 0 0 0</pose>
      <inertial>
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

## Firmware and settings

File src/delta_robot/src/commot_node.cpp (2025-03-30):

#include <iostream>
#include <chrono>
#include <functional>
#include <memory>
#include <string>
#include <cstdio>
#include <cmath>

#include "dynamixel_sdk/dynamixel_sdk.h"
#include "dynamixel_sdk_custom_interfaces/msg/set_position.hpp"
#include "dynamixel_sdk_custom_interfaces/srv/get_position.hpp"
#include "rclcpp/rclcpp.hpp"
#include "rcutils/cmdline_parser.h"

#include "../include/commot_node.hpp"

#include "delta_robot_interfaces/msg/op_mod.hpp"


// Control table address for X series 
#define ADDR_OPERATING_MODE 11
#define ADDR_TORQUE_ENABLE 64
#define ADDR_GOAL_POSITION 116
#define ADDR_PRESENT_POSITION 132

#define ADDR_VEL_I_GAIN 76
#define ADDR_VEL_P_GAIN 78
#define ADDR_POS_P_GAIN 84
#define ADDR_POS_I_GAIN 82
#define ADDR_POS_D_GAIN 80

// Protocol version
#define PROTOCOL_VERSION 2.0  // Default Protocol version of DYNAMIXEL X series.

// Default setting
#define BAUDRATE 57600  // Default Baudrate of DYNAMIXEL X series
#define DEVICE_NAME "/dev/ttyUSB0"  //! [Linux]: "/dev/ttyUSBXXXXXXXX", [Windows]: "COM*"

dynamixel::PortHandler * portHandler;
dynamixel::PacketHandler * packetHandler;

uint8_t dxl_error = 0;
uint32_t goal_position = 0;
int dxl_comm_result = COMM_TX_FAIL;

commot::commot(): Node("COMMOT")
{
    //Test if Node is active
    RCLCPP_INFO(this->get_logger(), "Run COMMOT node");

    //Set rclpp Qualtiy of Servie parameters: depth, reliable mode and durabiltiy to volatile(=no storage)
    this->declare_parameter("qos_depth", 10);
    int8_t qos_depth = 0;
    this->get_parameter("qos_depth", qos_depth);
    const auto QOS_RKL10V =
        rclcpp::QoS(rclcpp::KeepLast(qos_depth)).reliable().durability_volatile();
    


    //?Goal Position setting and logging (topic based)
    set_position_subscriber_ =
    this->create_subscription<SetPosition>(
    "set_position",
    QOS_RKL10V,
    [this](const SetPosition::SharedPtr msg) -> void  //lambda function with capture of local class and void {functionality} return
    {
      uint8_t dxl_error = 0;

      // Position Value of X series is 4 byte data.
      uint32_t goal_position = (unsigned int)msg->position;  // Convert int32 -> uint32

      //* Write Goal Position (length : 4 bytes)
      // When writing 2 byte data to AX / MX(1.0), use write2ByteTxRx() instead.
      dxl_comm_result =
      packetHandler->write4ByteTxRx(    //write&read functions can be found in DynamixelSDK/dynamixel_sdk/include/dynamixel_sdk/protocol2_packet_handler.h
        portHandler,
        (uint8_t) msg->id,
        ADDR_GOAL_POSITION,
        goal_position,
        &dxl_error
      );
      //*=====> after writing the motor will move to goal position (if motor in position control mode)

      //Definition of logger output
      if (dxl_comm_result != COMM_SUCCESS) {
        RCLCPP_INFO(this->get_logger(), "%s", packetHandler->getTxRxResult(dxl_comm_result));
      } else if (dxl_error != 0) {
        RCLCPP_INFO(this->get_logger(), "%s", packetHandler->getRxPacketError(dxl_error));
      } else {
        RCLCPP_INFO(this->get_logger(), "Set [ID: %d] [Goal Position: %d]", msg->id, msg->position);
      }
    }
    );

    //?Reading and logging of current postion (service based)
    auto get_present_position =
      [this](
      const std::shared_ptr<GetPosition::Request> request,
      std::shared_ptr<GetPosition::Response> response) -> void
      {
        uint32_t present_position = 0;
        // Read Present Position (length : 4 bytes) and Convert uint32 -> int32
        dxl_comm_result = packetHandler->read4ByteTxRx(
          portHandler,
          (uint8_t) request->id,
          ADDR_PRESENT_POSITION,
          reinterpret_cast<uint32_t *>(&present_position),
          &dxl_error
        );
        /*
        RCLCPP_INFO(
          this->get_logger(),
          "Get [ID: %d] [Present Position: %d]",
          request->id,
          present_position
        );
        */
        response->position = present_position;
      };

    //create a service sever for the defined lambda function
    get_position_server_ = create_service<GetPosition>("get_position", get_present_position);
    


    //* Overall structure: sub for opmode message which conatains the variable "mode" decides between point navigation and compliant mode using a switch case. 
    //* Control parameters are set in each mode individually. In compliant mode an adaptive change of the control gains can be chosen.
   
    OpMod_subscriber_ =
    this->create_subscription<delta_robot_interfaces::msg::OpMod>(
    "OpMod",
    QOS_RKL10V,
    [this](const delta_robot_interfaces::msg::OpMod::SharedPtr msg) -> void  //lambda function with capture of local class and void {functionality} return
    {
      uint8_t dxl_error = 0;
      

      switch(msg->mode){
        case 0 :{             //* = point navigation mode
          int kpp = 800;
          int kdp = 8500;
          int start_position = 2692;
          
          for (int i =1; i<=3; i++){          //sequential setting of Motor control paramaters
          dxl_comm_result =
            packetHandler->write2ByteTxRx(    //write&read functions can be found in DynamixelSDK/dynamixel_sdk/include/dynamixel_sdk/protocol2_packet_handler.h
            portHandler,
            i,
            ADDR_POS_P_GAIN,
            kpp,
            &dxl_error);
                  
          dxl_comm_result =
            packetHandler->write2ByteTxRx(   
            portHandler, 
            i,
            ADDR_POS_D_GAIN,
            kdp,
            &dxl_error);
            
          dxl_comm_result =
            packetHandler->write4ByteTxRx(    
            portHandler,
            i,
            ADDR_GOAL_POSITION,
            start_position,
            &dxl_error);
          }

          break;
        }

        case 1 : {         //* compliant mode
  
          //! the home position of the robot for the compliant mode is chosen to the effector position of xeff=0, yeff=0 und z=300 => resulting in the 2692. Increment for all 3 motors 
          int home_position = 2692;

          for (int i =1; i<=3; i++){ 
          dxl_comm_result =
                  packetHandler->write2ByteTxRx(    
                    portHandler,
                    i,
                    ADDR_POS_D_GAIN,
                    0,
                    &dxl_error
                  );
          if (dxl_comm_result != COMM_SUCCESS) {
            RCLCPP_WARN(this->get_logger(), "Error with zeroing D-Gain of motor %d, breaking loop", i);
            break; }

          dxl_comm_result =
            packetHandler->write4ByteTxRx(    
            portHandler,
            i,
            ADDR_GOAL_POSITION,
            home_position,
            &dxl_error
          );
          if (dxl_comm_result != COMM_SUCCESS) {
            RCLCPP_WARN(this->get_logger(), "Error with writing Goal Position to motor %d, breaking loop", i);
            break; }
          }

          RCLCPP_INFO(rclcpp::get_logger("COMMOT"), "Succeeded to zero D-Gains and setting home position of all 3");


          for (int i =1; i<=3; i++){

          //! The code that is commented out below describes the adaptive motor gain control. The code works BUT there is a reliability issue when commot and opmod node are running.
          //! The problem appears to be realted to the high data traffic. Then packages might get lost between motor and the nodes which results in for-loops which arent't broken. 
          //! In the end this results in the ros2 node error "stack smash" which causes the node to crash.
          //! Antoher possibility is that the usage of a virtual machine is the root of the problem.

          //! Therefore the code which is commented out could be described as "experimental" but currently not robust.                         
          /*
          uint32_t present_position_i = 0;
          //reading present positions of the 3 motors
          dxl_comm_result = packetHandler->read4ByteTxRx(
            portHandler,
            i,
            ADDR_PRESENT_POSITION,
            reinterpret_cast<uint32_t *>(&present_position_i),
            &dxl_error
          );
          //Definition of logger output
          if (dxl_comm_result != COMM_SUCCESS) {
            RCLCPP_WARN(this->get_logger(), "Reading present Pos: %s, breaking loop", packetHandler->getTxRxResult(dxl_comm_result));
            break; }
            else if (dxl_error != 0) {
            RCLCPP_WARN(this->get_logger(), "Reading present Pos: %s, breaking loop", packetHandler->getRxPacketError(dxl_error));
            break; }
            else {
            RCLCPP_INFO(this->get_logger(), "Present [ID: %i]", i);
          }    
          
          //calculate difference between present_position and home-position and calculate Kp based on Kp(e) = 1000/((e-2)^0,75)
          int e = home_position-present_position_i;
          e = abs(e);
          //int e = static_cast<int>(std::max(home_position, present_position_i) - std::min(home_position, present_position_i));

          RCLCPP_INFO(this->get_logger(), "Present [ID: %i] [e: %i]", i, e);
          float maxkp = 200.0;
          
          //float kpc = (abs(e) > 0) ? 1.5*(pow(10.0,(static_cast<double>(abs(e)))/150.0))+0.15*static_cast<double>(abs(e))+10.0 : (maxkp-180); //*non-linear adaptive gain possibly better than normal linear function if parameters are set correctly
                   
          float kpc = (e > 0) ? 0.25*(static_cast<double>(e))+10.0 : (maxkp-180.0);  //* linear adaptive gain 
          if (kpc > maxkp){
            kpc = maxkp;
          }
          */

          //! Since the adaptive gain control is currently not robust, the motor P-Gain is set constant to reduce the data traffic on the RS485 bus. 
          //! The constant P-Gain allows a compliant behaviour but with less accuracy then with adaptive gain control.
          //write new Kp to motors
          dxl_comm_result =
          packetHandler-> write2ByteTxRx(    
            portHandler,
            i,
            ADDR_POS_P_GAIN,
            25,                          //! If adaptive gain control ("experimental code" above) is used, the 25 has to be replaced by: " static_cast<uint32_t>(std::round(kpc)), "
            &dxl_error
          );
          
          if (dxl_comm_result != COMM_SUCCESS) {
            RCLCPP_WARN(this->get_logger(), "Writing kpc: %s, breaking loop", packetHandler->getTxRxResult(dxl_comm_result));
            break; }
            else if (dxl_error != 0) {
            RCLCPP_WARN(this->get_logger(), "Writing kpc: %s, breaking loop", packetHandler->getRxPacketError(dxl_error));
            break; }
           else {
            RCLCPP_INFO(this->get_logger(), "Present [ID: %i] ", i);
          }     
          }
          break;
        }

        default:
          RCLCPP_ERROR(rclcpp::get_logger("COMMOT"), "No Operating Mode was chosen");
          break;
      
      }
    }
    );
}

commot::~commot()
{
}

void setupDynamixel(uint8_t dxl_id)
{
  // Use Position Control Mode
  dxl_comm_result = packetHandler->write1ByteTxRx(
    portHandler,
    dxl_id,
    ADDR_OPERATING_MODE,
    5,   //current-based position control was chosen => needed for compliant mode and smoother in point navigation mode than position control mode
    &dxl_error
  );

  if (dxl_comm_result != COMM_SUCCESS) {
    RCLCPP_ERROR(rclcpp::get_logger("COMMOT"), "Failed to set Position Control Mode.");
  } else {
    RCLCPP_INFO(rclcpp::get_logger("COMMOT"), "Succeeded to set Position Control Mode.");
  }

  // Enable Torque of DYNAMIXEL
  dxl_comm_result = packetHandler->write1ByteTxRx(  
    portHandler,
    dxl_id,
    ADDR_TORQUE_ENABLE,
    1,
    &dxl_error
  );

  if (dxl_comm_result != COMM_SUCCESS) {
    RCLCPP_ERROR(rclcpp::get_logger("COMMOT"), "Failed to enable torque.");
  } else {
    RCLCPP_INFO(rclcpp::get_logger("COMMOT"), "Succeeded to enable torque.");
  }
}

int main(int argc, char * argv[])
{
  portHandler = dynamixel::PortHandler::getPortHandler(DEVICE_NAME);
  packetHandler = dynamixel::PacketHandler::getPacketHandler(PROTOCOL_VERSION);

  // Open Serial Port
  dxl_comm_result = portHandler->openPort();
  if (dxl_comm_result == false) {
    RCLCPP_ERROR(rclcpp::get_logger("COMMOT"), "Failed to open the port!");
    return -1;
  } else {
    RCLCPP_INFO(rclcpp::get_logger("COMMOT"), "Succeeded to open the port.");
  }

  // Set the baudrate of the serial port (use DYNAMIXEL Baudrate)
  dxl_comm_result = portHandler->setBaudRate(BAUDRATE);
  if (dxl_comm_result == false) {
    RCLCPP_ERROR(rclcpp::get_logger("COMMOT"), "Failed to set the baudrate!");
    return -1;
  } else {
    RCLCPP_INFO(rclcpp::get_logger("COMMOT"), "Succeeded to set the baudrate.");
  }

  setupDynamixel(BROADCAST_ID);

  rclcpp::init(argc, argv);

  for (int m =1; m<=3; m++){
            dxl_comm_result =
                    packetHandler->write2ByteTxRx(    
                      portHandler,
                      m,
                      ADDR_VEL_I_GAIN,
                      0,                          
                      &dxl_error
                    );
            dxl_comm_result =
            packetHandler->write2ByteTxRx(    
              portHandler,
              m,
              ADDR_VEL_P_GAIN,
              0,                          
              &dxl_error
            );
            dxl_comm_result =
                  packetHandler->write2ByteTxRx(    
                    portHandler,
                    m,
                    ADDR_POS_D_GAIN,
                    0,
                    &dxl_error
                  );
    RCLCPP_INFO(rclcpp::get_logger("COMMOT"), "Succeeded to zero Vel-Gains and D-Gain of ID %i.", m);
  } 

  auto commot_start = std::make_shared<commot>();
  rclcpp::spin(commot_start);
  rclcpp::shutdown();

  // Disable Torque of DYNAMIXEL
  packetHandler->write1ByteTxRx(
    portHandler,
    BROADCAST_ID,
    ADDR_TORQUE_ENABLE,
    0,
    &dxl_error
  );

  return 0;
}

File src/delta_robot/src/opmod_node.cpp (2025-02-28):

#include <iostream>
#include <chrono>
#include <functional>
#include <memory>
#include <string>
#include <cstdio>
#include <array>

#include "dynamixel_sdk/dynamixel_sdk.h"

#include "dynamixel_sdk_custom_interfaces/msg/set_position.hpp"
#include "dynamixel_sdk_custom_interfaces/srv/get_position.hpp"

#include "delta_robot_interfaces/msg/op_mod.hpp"

#include "geometry_msgs/msg/twist.hpp"

#include "rclcpp/rclcpp.hpp"
#include "rcutils/cmdline_parser.h"

#include <kinematics.h>

using namespace std::chrono_literals;
using std::placeholders::_1;


class opmod : public rclcpp::Node 
{
    public:
    opmod() : Node("OPMOD")
    {
    RCLCPP_INFO(this->get_logger(), "Run OPMOD node");
    auto logger = this->get_logger();
        //Set rclpp Qualtiy of Servie parameters: depth, reliable mode and durabiltiy to volatile(=no storage)
    this->declare_parameter("qos_depth", 10);
    int8_t qos_depth = 0;
    this->get_parameter("qos_depth", qos_depth);
    const auto QOS_RKL10V =
        rclcpp::QoS(rclcpp::KeepLast(qos_depth)).reliable().durability_volatile();

 

    _subOpMod = this -> create_subscription<delta_robot_interfaces::msg::OpMod>("OpMod", 1, std::bind(&opmod::callbackMODE, this, _1));


    _pubGoalPosMotor = this -> create_publisher<dynamixel_sdk_custom_interfaces::msg::SetPosition>("set_position",QOS_RKL10V);

    pos_client = this -> create_client<dynamixel_sdk_custom_interfaces::srv::GetPosition>("get_position");

    _TimerDirection = this->create_wall_timer(std::chrono::milliseconds(50),std::bind(&opmod::callbackTimerDirection, this));
    _pubDirection = this -> create_publisher<geometry_msgs::msg::Twist>("cmd_vel",QOS_RKL10V);  //! topic name has to be equal to topic name which the mobile robot subscribes to
    
    
    
    }

    private:
        void callbackMODE (const delta_robot_interfaces::msg::OpMod msg){
            
            switch (msg.mode){
                case 0:{

                    mode = 0;
                    //Definition of logger output
                    RCLCPP_INFO(this->get_logger(), "Recieved Goal Position [xeff: %f] [yeff: %f] [zeff: %f]", msg.xeff, msg.yeff, msg.zeff);
                        
                    float xeffmsg = msg.xeff;
                    float yeffmsg = msg.yeff;
                    float zeffmsg = -msg.zeff; //kinematics is based on a normal delta robot => needs a neg. z coord but in this case it's more intuitive to set a positive z coord

                        

                    int (&invkinout)[3][3] = invkin(xeffmsg,yeffmsg, zeffmsg);
                    RCLCPP_INFO(this->get_logger(), "Calculated Motor Angles [xeff: %d] [yeff: %d] [zeff: %d]", invkinout [0][2], invkinout [1][2], invkinout [2][2]);
                    RCLCPP_INFO(this->get_logger(), "Calculated Motor Positions [xeff: %d] [yeff: %d] [zeff: %d]", invkinout [0][1], invkinout [1][1], invkinout [2][1]);

                    out1.id         =invkinout [0][0];
                    out1.position   =invkinout [0][1];
                    out2.id         =invkinout [1][0];
                    out2.position   =invkinout [1][1];
                    out3.id         =invkinout [2][0];
                    out3.position   =invkinout [2][1];
                        

                    _pubGoalPosMotor -> publish(out1);
                    _pubGoalPosMotor -> publish(out2);
                    _pubGoalPosMotor -> publish(out3);

                    RCLCPP_INFO(this->get_logger(), "Calculated Motor Positions [ID: %d] [Position: %d] [ID: %d] [Position: %d] [ID: %d] [Position: %d]", out1.id , out1.position , out2.id, out2.position, out3.id, out3.position);
                    break;                
                }

                case 1:{

                    mode = 1;
                    
                    for (int i = 0; i <= 2; i++) {
                        auto req_motor_i = std::make_shared<dynamixel_sdk_custom_interfaces::srv::GetPosition::Request>();
                        req_motor_i->id = i + 1;
                        
                        // Wait for service to be available
                        while (!pos_client->wait_for_service(1s)) {
                            if (!rclcpp::ok()) {
                                RCLCPP_ERROR(rclcpp::get_logger("rclcpp"), "Interrupted while waiting for the service. Exiting.");
                                return; // Exit if ROS is not ok
                            }
                            RCLCPP_INFO(rclcpp::get_logger("rclcpp"), "Service not available, waiting again...");
                        }
                        
                        auto result_future = pos_client->async_send_request(req_motor_i, 
                        [this,i](rclcpp::Client<dynamixel_sdk_custom_interfaces::srv::GetPosition>::SharedFuture future) {
                            auto result = future.get();
                            //RCLCPP_INFO(this->get_logger(), "Position recieved [position: %d]", result->position);
                            fwdkin_in [i] = result -> position;   
                        });

                    }
                    
                    RCLCPP_INFO(this->get_logger(), "Position recieved [position1: %d][position2: %d][position3: %d]", fwdkin_in [0], fwdkin_in [1], fwdkin_in [2]);

                    fwdkinout = fwdkin(fwdkin_in[0], fwdkin_in[1], fwdkin_in[2]);
                    
                    break;  
                }
            }
        }

    void callbackTimerDirection()
        {
            if (mode == 1){
            geometry_msgs::msg::Twist twist;
                    twist.linear.x = fwdkinout[0];
                    twist.linear.y = fwdkinout[1];
                    twist.linear.z = fwdkinout[2];
                    _pubDirection -> publish(twist);
            }
        
        }

    dynamixel_sdk_custom_interfaces::msg::SetPosition out1;
    dynamixel_sdk_custom_interfaces::msg::SetPosition out2;
    dynamixel_sdk_custom_interfaces::msg::SetPosition out3;


    rclcpp::Subscription<delta_robot_interfaces::msg::OpMod>::SharedPtr _subOpMod;
    rclcpp::Publisher<dynamixel_sdk_custom_interfaces::msg::SetPosition>::SharedPtr _pubGoalPosMotor;
    rclcpp::Publisher<geometry_msgs::msg::Twist>::SharedPtr _pubDirection;
    rclcpp::Client<dynamixel_sdk_custom_interfaces::srv::GetPosition>::SharedPtr pos_client;
    rclcpp::TimerBase::SharedPtr _TimerDirection;

    std::array<int, 3> fwdkin_in;
    std::array<float, 3> fwdkinout;
   
    int mode;

};


int main (int argc, char *argv[])
{
    rclcpp::init(argc, argv);
    auto opmod_start = std::make_shared<opmod>();
    rclcpp::spin(opmod_start);
    rclcpp::shutdown();
    return 0;
}

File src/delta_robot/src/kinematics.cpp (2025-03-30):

#include <iostream>
#include <math.h>
#include <array>
#include <stdio.h>
#include <cmath>
//? based on: https://hypertriangle.com/~alex/delta-robot-tutorial/  

#define PI  3.14159265
#define dtr  0.017453293  //from deg to rad
#define sin30  0.5
#define sin120  0.8660254
#define sinm120 -0.866025
#define cos120  -0.5      //= cos(-120)
#define tan30  0.57735027
#define tan60  1.7320508

using namespace std;

//! Radii must be set according to the position of the intersection of the arm's symmetry axis
//! with the axis of either the motorshaft or the endeffector joint shaft!
float re = 30.0;  //effector radius in mm
float rf = 95.0; //base radius in mm
float e = 2*re*tan60;  //length of triangle side of endeffector
float f = 2*rf*tan60;  //length of triangle side of base
float deg2pulse = 4096.0 / 360.0;

float le = 300.0; //effector arm ("forearm") lenght in mm
float lf = 200.0; //base arm ("biceps") lenght in mm

int invout [3][3] = {{1,5,0},{2,5,0},{3,5,0}};
float prevangle [3] = {0,0,0}; //array that stores the theta angles of the previous inverse calculation 
std::array<float, 3> poseff = {0,0,0};
std::array<float, 3> prevposition = {1,0,5}; //array that stores the theta angles of the previous forward calculation 
int i = 0; 

float minangle = -30.0;
float maxangle = 90.0;

//?------forward kinematics-------
//? input the current angles theta of the motors 1,2,3 and return the current position of the endeffector (poseff)
std::array<float, 3> fwdkin(int motpos1, int motpos2, int motpos3) {

    float t = (f-e)*tan30/2; //Delta of the distance from the base (f) and effector (e) sides to z axis (common centerpoint of the triangles in start position)
    
    float theta1 = -dtr*((motpos1*(1/deg2pulse))-270);  
    float theta2 = -dtr*((motpos2*(1/deg2pulse))-270);
    float theta3 = -dtr*((motpos3*(1/deg2pulse))-270);      

    //Calculation of the joint positions with joint1 in the yz-plane and the other arms 30° rotated to relative to the x-axis
    float  y1 = -(t + lf*cos(theta1));
    float z1 = -lf*sin(theta1);
    
    float y2 = (t + lf*cos(theta2))*sin30;
    float  x2 = y2*tan60;
    float z2 = -lf*sin(theta2);
    
    float y3 = (t + lf*cos(theta3))*sin30;
    float x3 = -y3*tan60;
    float z3 = -lf*sin(theta3);
    
    //*One spheres around each joint with radius re  >>> (sphere1-sphere2) & (sphere1-sphere3) & (sphere2-sphere3) 
    //* >>> isolate y and x in (s2-s3) seperately >>> substitute y in (s1-32) to get x (I) & substitute x in (s1-s3) to get y (II)
    float w1 = y1*y1 + z1*z1;            //extra variables w to short the following equations
    float w2 = x2*x2 + y2*y2 + z2*z2;
    float w3 = x3*x3 + y3*y3 + z3*z3;

    float dnm = (y2-y1)*x3-(y3-y1)*x2;

    //* (I) x = (a1*z + b1)/dnm
    float a1 = (z2-z1)*(y3-y1)-(z3-z1)*(y2-y1);
    float b1 = -((w2-w1)*(y3-y1)-(w3-w1)*(y2-y1))/(float)2.0;
 
    //* (II) y = (a2*z + b2)/dnm;
    float a2 = -(z2-z1)*x3+(z3-z1)*x2;
    float b2 = ((w2-w1)*x3 - (w3-w1)*x2)/(float)2.0;
 
    //* Substitute y and x in the equation for sphere1 and solve the resulting quadratic equation to get z
    float a = a1*a1 + a2*a2 + dnm*dnm;
    float b = 2*(a1*b1 + a2*(b2-y1*dnm) - z1*dnm*dnm);
    float c = (b2-y1*dnm)*(b2-y1*dnm) + b1*b1 + dnm*dnm*(z1*z1 - le*le); 
  
    // discriminant
    float d = b*b - (float)4.0*a*c;
    if (d < 0) return prevposition; // if current calculation of end-effector position is somehow false return previous calculated position back to OPMOD node
   
   
    //resulting coords of the effector
    float zeff = -0.5*(b+sqrt(d))/a;
    float xeff = (a1*zeff + b1)/dnm;
    float yeff = (a2*zeff + b2)/dnm;
   
    prevposition [0] = 0.003*xeff;
    prevposition [1] = 0.003*yeff;
    prevposition [2] = -zeff;
    
   //Twist is 0 when the deflection in x or y is greater than 3 cm => otherwise robot will not stand still since there will always be little deflection
   if (abs(xeff) < 30){ 
      xeff = 0;
   }
   if (abs(yeff) < 30){
      yeff = 0;
   }
   
    poseff[0] = 0.003*xeff; //factor controlls speed of the mobile robot
    poseff[1] = 0.003*yeff;
    poseff[2] = -zeff;
 
    return poseff;
}


//helper function for calculating the motorangles theta (by reference)
float delta_calcAngleYZ(float xeff, float yeff, float zeff, int i) { 
     
     float y1 = -0.5* tan30*f;  // get coords of motorshaft1 which lies in the yz-plane
     yeff -= 0.5*tan30*e;         // shift effector center to edge perpendicular to yz-plane

     // z = a + b*y | linear equation via subtraction of the 2 circle equations and solve after z
     float a = (xeff*xeff + yeff*yeff + zeff*zeff +lf*lf - le*le - y1*y1)/(2*zeff);
     float b = (y1-yeff)/zeff;

     //substitute the lin. eq. back into one of the 2 circle equations and compute the discriminant
     float d = -((a+b*y1)*(a+b*y1))+lf*(b*b*lf+lf); 
     if (d < 0) return prevangle[i]; //! if non-reachable point with the given kinematics => then biceps will stay in previous position

     float yj = (y1 - a*b - sqrt(d))/(b*b + 1); // choosing outer point (= - branch of the quadratic equation)
     float zj = a + b*yj;
     float theta = 180.0*atan(-zj/(y1 - yj))/PI; //Output in Degree
     if (theta < -30 || theta >= 90)
        return prevangle[i];
     else 
        return theta;
 }

//?------inverse kinematics-------
//? input the goal endeffector position (poseff) and return goal angles theta of the motors 1,2,3 
//? function referencing the array invout to be able to return invout afterwards
int (&invkin(float xeff, float yeff, float zeff))[3][3]{
     i = 0;   
     float theta1 = delta_calcAngleYZ(xeff, yeff, zeff, i);
     i++;
     float theta2 = delta_calcAngleYZ(xeff*cos120 + yeff*sin120, yeff*cos120-xeff*sin120, zeff, i);  // rotate coords to +120 deg via multiplication with (standard) rotation matrix
     i++;
     float theta3 = delta_calcAngleYZ(xeff*cos120 - yeff*sin120, yeff*cos120+xeff*sin120, zeff, i);  // rotate coords to -120 deg via multiplication with(standard) rotation matrix

     prevangle [0] = theta1;
     prevangle [1] = theta2;
     prevangle [2] = theta3;
      
     float angle1 = ((-theta1+270.0)*deg2pulse); //+270 so that negative motorpoitions (0...4095) are avoided
     float angle2 = ((-theta2+270.0)*deg2pulse); 
     float angle3 = ((-theta3+270.0)*deg2pulse);

     int posmotor1 = static_cast<int>(round(angle1));
     int posmotor2 = static_cast<int>(round(angle2));
     int posmotor3 = static_cast<int>(round(angle3));

     invout[0][1] = posmotor1;
     invout[1][1] = posmotor2;
     invout[2][1] = posmotor3;
     invout[0][2] = theta1;
     invout[1][2] = theta2;
     invout[2][2] = theta3;

     return invout;
}

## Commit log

2024-12-15 commot fixed and started opmod incl. custom interfaces
    [commot_node.cpp, kinematics.cpp]
2024-12-17 Debugging with conntected Hardware - neg. angles not allowed still needs fix
    [commot_node.cpp, kinematics.cpp, opmod_node.cpp]
2024-12-19 hardware test success with all 3 motors(without arms attached) (no false and negative angles)
2024-12-19 if non-reachable point motors will remain in previous calculated position
2025-03-30 sim package,readme and matlab & stl files added
    [63755205_1.stl, 63755205_2.stl, 63755205_3.stl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]
